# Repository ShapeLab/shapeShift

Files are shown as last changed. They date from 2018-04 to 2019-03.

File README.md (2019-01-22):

## shapeShift: 2D Spatial Manipulation and Self-Actuation of Tabletop Shape Displays for Tangible and Haptic Interaction 

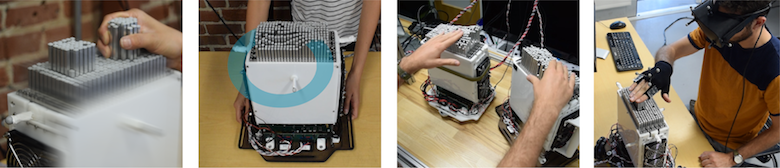
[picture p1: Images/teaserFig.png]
Teaser


We explore interactions enabled by 2D spatial manipulation and self-actuation of a tabletop shape display. To explore these interactions, we developed shapeShift, a compact, high-resolution (7 mm pitch), mobile tabletop shape display. shapeShift can be mounted on passive rollers allowing for bimanual interaction where the user can freely manipulate the system while it renders spatially relevant content. shapeShift can also be mounted on an omnidirectional-robot to provide both vertical and lateral kinesthetic feedback, display moving objects, or act as an encountered-type haptic device for VR. We present a study on haptic search tasks comparing spatial manipulation of a shape display for egocentric exploration of a map versus exploration using a fixed display and a touch pad. Results show a 30% decrease in navigation path lengths, 24% decrease in task time, 15% decrease in mental demand and 29% decrease in frustration in favor of egocentric navigation. 

[Watch a video](https://www.youtube.com/embed/Z6LSsJoDdtY/0.jpg) or read more at the [shape lab website](http://shape.stanford.edu/research/shapeShift/)

### Technical Implementation
<p align="center">
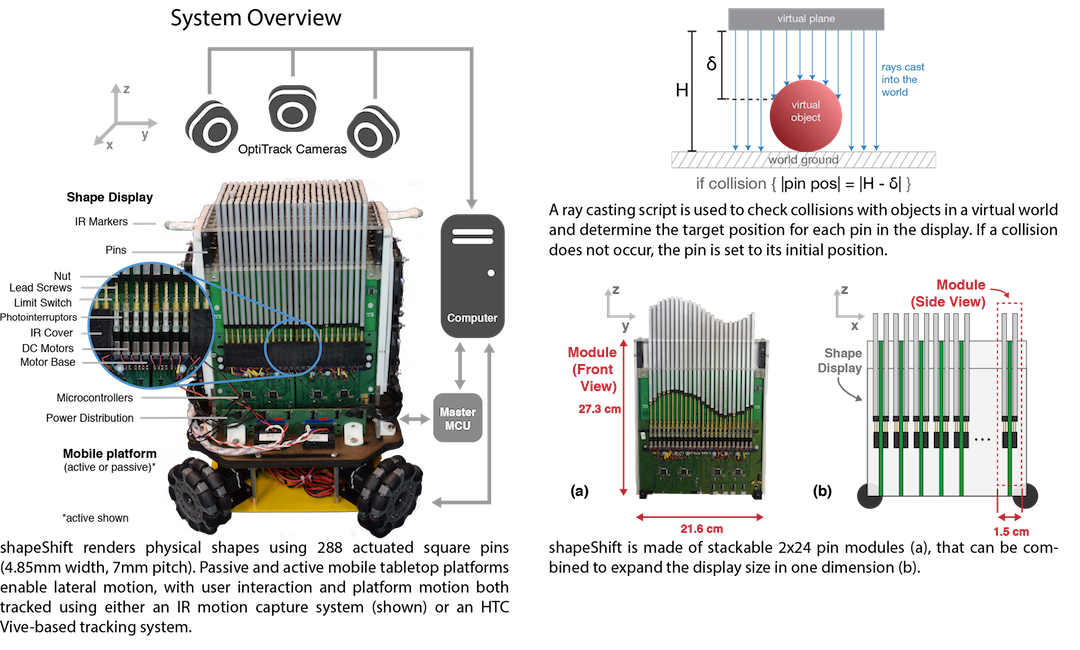
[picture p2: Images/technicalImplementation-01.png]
exploded
	
</p>

### Getting started
CAD, PCB, firmware and software files are provided. Detailed instructions and link to BOM can be found in [these slides](https://docs.google.com/presentation/d/1R9Z0mCOPYOkJPzbJNwtG9fEYhSLC97248hX_nJxPLbI/edit?usp=sharing).

### Latest Updates
- Released PCB + CAD files + Firmware
- Unity software coming soon

### Authors
[Alexa F. Siu](http://alexasiu.com), Eric J. Gonzalez, Shenli Yuan, Jason B. Ginsberg, and Sean Follmer

### Contact
Raise a new [issue](https://github.com/ShapeLab/shapeShift/issues) or contact me at afsiu@stanford.edu

<br>

<p align="center">
	<br />This work is licensed under a <a rel="license" href="http://creativecommons.org/licenses/by-nc/4.0/">Creative Commons Attribution-NonCommercial 4.0 International License</a>.
</p>

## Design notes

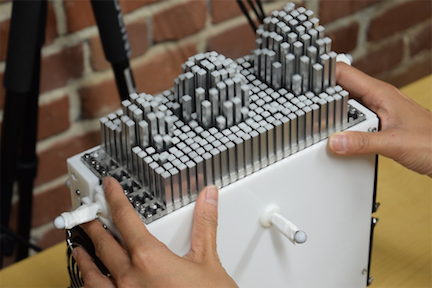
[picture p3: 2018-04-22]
Images/main.png

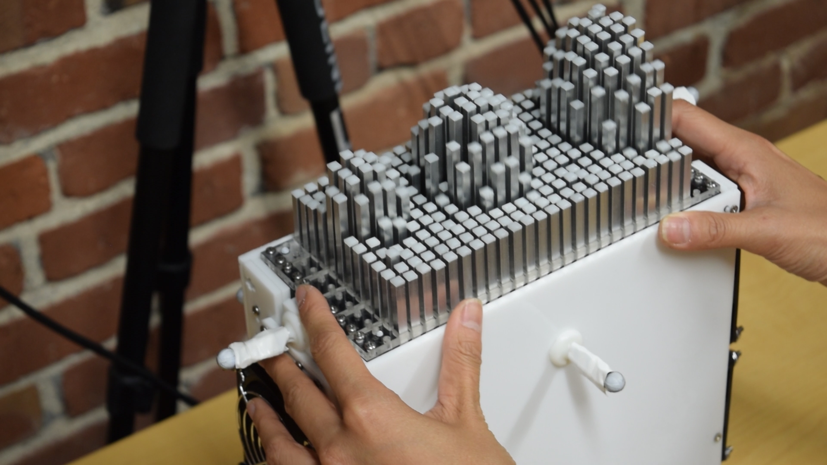
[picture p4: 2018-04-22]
Images/main3.png

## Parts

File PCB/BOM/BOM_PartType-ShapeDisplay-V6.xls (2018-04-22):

Comment | Description | Designator | Footprint | LibRef | Quantity | Comment
Murata GRM155R71C104KA88J | Multilayer Ceramic Capacitors MLCC - SMD/SMT 0.1uF 16 volts 10% | C1, C2_SH1, C2_SH2, C2_SH3, C2_SH4, C2_SH5, C2_SH6, C2_SH7, C2_SH8, C2_SH9, C2_SH10, C2_SH11, C2_SH12, C2_SH13, C2_SH14, C2_SH15, C2_SH16, C2_SH17, C2_SH18, C2_SH19, C2_SH20, C2_SH21, C2_SH22, C2_SH23, C2_SH24, C2_SH25, C2_SH26, C2_SH27, C2_SH28, C2_SH29, C2_SH30, C2_SH31, C2_SH32, C2_SH33, C2_SH34, C2_SH35, C2_SH36, C2_SH37, C2_SH38, C2_SH39, C2_SH40, C2_SH41, C2_SH42, C2_SH43, C2_SH44, C2_SH45, C2_SH46, C2_SH47, C2_SH48, C3_SH1, C3_SH2, C3_SH3, C3_SH4, C3_SH5, C3_SH6, C3_SH7, C3_SH8, C3_SH9, C3_SH10, C3_SH11, C3_SH12, C3_SH13, C3_SH14, C3_SH15, C3_SH16, C3_SH17, C3_SH18, C3_SH19, C3_SH20, C3_SH21, C3_SH22, C3_SH23, C3_SH24, C3_SH25, C3_SH26, C3_SH27, C3_SH28, C3_SH29, C3_SH30, C3_SH31, C3_SH32, C3_SH33, C3_SH34, C3_SH35, C3_SH36, C3_SH37, C3_SH38, C3_SH39, C3_SH40, C3_SH41, C3_SH42, C3_SH43, C3_SH44, C3_SH45, C3_SH46, C3_SH47, C3_SH48, C7, C8, C9, C11, C12, C13, C14, C15, C18, C19, C20, C21, C22, C23, C24, C26, C28, C29, C30, C32, C33, C34, C36, C37, C39, C40, C41, C42, C301 | CAPC1005X55X25NL05T10 | CMP-131530-4, CMP-131530-5, CMP-131530-5, CMP-131530-5, CMP-131530-5, CMP-131530-5, CMP-131530-5, CMP-131530-5, CMP-131530-5, CMP-131530-5, CMP-131530-5, CMP-131530-5, CMP-131530-5, CMP-131530-5, CMP-131530-5, CMP-131530-5, CMP-131530-5, CMP-131530-5, CMP-131530-5, CMP-131530-5, CMP-131530-5, CMP-131530-5, CMP-131530-5, CMP-131530-5, CMP-131530-5, CMP-131530-5, CMP-131530-5, CMP-131530-5, CMP-131530-5, CMP-131530-5, CMP-131530-5, CMP-131530-5, CMP-131530-5, CMP-131530-5, CMP-131530-5, CMP-131530-5, CMP-131530-5, CMP-131530-5, CMP-131530-5, CMP-131530-5, CMP-131530-5, CMP-131530-5, CMP-131530-5, CMP-131530-5, CMP-131530-5, CMP-131530-5, CMP-131530-5, CMP-131530-5, CMP-131530-5, CMP-131530-4, CMP-131530-4, CMP-131530-4, CMP-131530-4, CMP-131530-4, CMP-131530-4, CMP-131530-4, CMP-131530-4, CMP-131530-4, CMP-131530-4, CMP-131530-4, CMP-131530-4, CMP-131530-4, CMP-131530-4, CMP-131530-4, CMP-131530-4, CMP-131530-4, CMP-131530-4, CMP-131530-4, CMP-131530-4, CMP-131530-4, CMP-131530-4, CMP-131530-4, CMP-131530-4, CMP-131530-4, CMP-131530-4, CMP-131530-4, CMP-131530-4, CMP-131530-4, CMP-131530-4, CMP-131530-4, CMP-131530-4, CMP-131530-4, CMP-131530-4, CMP-131530-4, CMP-131530-4, CMP-131530-4, CMP-131530-4, CMP-131530-4, CMP-131530-4, CMP-131530-4, CMP-131530-4, CMP-131530-4, CMP-131530-4, CMP-131530-4, CMP-131530-4, CMP-131530-4, CMP-131530-4, CMP-131530-4, CMP-131530-4, CMP-131530-4, CMP-131530-4, CMP-131530-4, CMP-131530-4, CMP-131530-4, CMP-131530-4, CMP-131530-4, CMP-131530-4, 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 | 126
Kemet T491D107K010AT | Capacitor, Tantalum, 100 uF, +/- 10%, -55 to 125 degC, 2-Pin SMD, RoHS, Tape and Reel | C4, C5 | KEMT-T491-D_M | CMP-19303020-3 | 2
AVX Interconnect / Elco 04024D225MAT2A | Multilayer Ceramic Capacitors MLCC - SMD/SMT 0402 2.2uF 4volts Z5U 20% | C6, C10, C16, C17, C25, C27, C31, C35 | CAPC1005X56X25NL10T15 | CMP-126964-2 | 8
Murata GRM155R60E106ME16D | MURATA GRM155R60E106ME16D CAP, MLCC, X5R, 10UF, 2.5V, 0402 | C38_M1, C38_M2, C38_M3, C38_M4, C38_M5, C38_M6, C38_M7, C38_M8, C38_M9, C38_M10, C38_M11, C38_M12 | CAPC1005X55X25LL05T10 | CMP-4845683-2 | 12
Murata GRM188R61A105KA61D | Cap Ceramic 1uF 10V X5R 10% SMD 0603 85°C Paper T/R | C300 | PCB-5ad2x2bi7uvqy4h6r523-1 | CMP-bc9f7597675b6358-1 | 1
Avago HSMA-C190 | LED 595NM AMB DIFF 0603 SMD | DS1, DS2, DS3, DS4 | AVAG-HSMX-C190 | CMP-1545179-2 | 4
BLM18AG601SN1D | Chip Ferrite Bead for General Use, 600 Ohm, 500 mA, -55 to 125 degC, 1.6 x 0.8 x 0.95 mm SMD, Tape and Reel | FB1, FB2, FB3, FB4, FB5, FB6, FB7, FB8 | MURA-BLM18-F-H1-CHIP-2_V | CMP-14419471-3 | 8
Motor Pads (DO NOT PLACE) | 0.1 Motor Header" | P1_M1, P1_M2, P1_M3, P1_M4, P1_M5, P1_M6, P1_M7, P1_M8, P1_M9, P1_M10, P1_M11, P1_M12, P2_M1, P2_M2, P2_M3, P2_M4, P2_M5, P2_M6, P2_M7, P2_M8, P2_M9, P2_M10, P2_M11, P2_M12 | PCB-xvvcuqhn1e5czmkfuo8y-1 | CMP-8f9uj9jvfkpvtxocz57i-8 | 24 | Do not place this component. These are just solder pads for the motor thus there is no associated component required for PCB pick and place
Molex 504050-0491 | 1, 50mm Pitch Pico-Lock Surface Mount Wire-to-Board Header, Right Angle, 2, 00mm Mated Height, Positive Side Locks, 4... | P3, P4 | PCB-3hbjo6f1kjza7fe1cyp7-1 | CMP-a06768b592477fa0-1 | 2
Molex 504050-0691 | Conn Wire to Board HDR 6 POS 1.5mm Solder RA SMD Pico-Lock? ????? ? T/R | PP1 | PCB-qm61l72v4f69z34pnmbq-1 | CMP-6c2ba4f309ebb3ec-1 | 1
Sharp GP2S60 | GP2S Series 0.5 mm 930 nm 35 V 50 mA SMT Compact Reflective Photointerrupter | Q1_SH1, Q1_SH2, Q1_SH3, Q1_SH4, Q1_SH5, Q1_SH6, Q1_SH7, Q1_SH8, Q1_SH9, Q1_SH10, Q1_SH11, Q1_SH12, Q1_SH13, Q1_SH14, Q1_SH15, Q1_SH16, Q1_SH17, Q1_SH18, Q1_SH19, Q1_SH20, Q1_SH21, Q1_SH22, Q1_SH23, Q1_SH24, Q1_SH25, Q1_SH26, Q1_SH27, Q1_SH28, Q1_SH29, Q1_SH30, Q1_SH31, Q1_SH32, Q1_SH33, Q1_SH34, Q1_SH35, Q1_SH36, Q1_SH37, Q1_SH38, Q1_SH39, Q1_SH40, Q1_SH41, Q1_SH42, Q1_SH43, Q1_SH44, Q1_SH45, Q1_SH46, Q1_SH47, Q1_SH48 | PCB-8czhrdy28ouaryjd2oxu-1 | CMP-2bace0f94d51f46b-9 | 48
Panasonic / Panasonic ECG ERJ-2RKF1003X | Resistor Thick Film 0402 100k Ohm 1% 1-10 Watt ±100ppm °C Surface Mount Punched Carrier Tape and Reel | R1, R20_SH1, R20_SH2, R20_SH3, R20_SH4, R20_SH5, R20_SH6, R20_SH7, R20_SH8, R20_SH9, R20_SH10, R20_SH11, R20_SH12, R20_SH13, R20_SH14, R20_SH15, R20_SH16, R20_SH17, R20_SH18, R20_SH19, R20_SH20, R20_SH21, R20_SH22, R20_SH23, R20_SH24, R20_SH25, R20_SH26, R20_SH27, R20_SH28, R20_SH29, R20_SH30, R20_SH31, R20_SH32, R20_SH33, R20_SH34, R20_SH35, R20_SH36, R20_SH37, R20_SH38, R20_SH39, R20_SH40, R20_SH41, R20_SH42, R20_SH43, R20_SH44, R20_SH45, R20_SH46, R20_SH47, R20_SH48, R200 | 0402R | CMP-3656264-6 | 50
Panasonic / Panasonic ECG ERJ-2RKF1002X | Res Thick Film 0402 10K Ohm 1% 0.1W(1/10W) ±100ppm/°C Molded SMD Punched Carrier T/R | R3, R4, R5, R6, R7, R8, R9, R10, R11, R12, R13, R14, R23 | 0402-RES | CMP-4843210-4 | 13
Panasonic ERJ-2RKF4702X | Res Thick Film 0402 47K Ohm 1% 0.1W(1/10W) ±100ppm/C Molded SMD Automotive Punched T/R | R15_SH1, R15_SH2, R15_SH3, R15_SH4, R15_SH5, R15_SH6, R15_SH7, R15_SH8, R15_SH9, R15_SH10, R15_SH11, R15_SH12, R15_SH13, R15_SH14, R15_SH15, R15_SH16, R15_SH17, R15_SH18, R15_SH19, R15_SH20, R15_SH21, R15_SH22, R15_SH23, R15_SH24, R15_SH25, R15_SH26, R15_SH27, R15_SH28, R15_SH29, R15_SH30, R15_SH31, R15_SH32, R15_SH33, R15_SH34, R15_SH35, R15_SH36, R15_SH37, R15_SH38, R15_SH39, R15_SH40, R15_SH41, R15_SH42, R15_SH43, R15_SH44, R15_SH45, R15_SH46, R15_SH47, R15_SH48 | PCB-tt2uar11avl7c0hq0m8y-1 | CMP-8bf24267710c5435-2 | 48
Panasonic ERJ-2GEJ224X | Thick Film Resistors - SMD 0402 220Kohms 5% Tol | R16_SH1, R16_SH2, R16_SH3, R16_SH4, R16_SH5, R16_SH6, R16_SH7, R16_SH8, R16_SH9, R16_SH10, R16_SH11, R16_SH12, R16_SH13, R16_SH14, R16_SH15, R16_SH16, R16_SH17, R16_SH18, R16_SH19, R16_SH20, R16_SH21, R16_SH22, R16_SH23, R16_SH24, R16_SH25, R16_SH26, R16_SH27, R16_SH28, R16_SH29, R16_SH30, R16_SH31, R16_SH32, R16_SH33, R16_SH34, R16_SH35, R16_SH36, R16_SH37, R16_SH38, R16_SH39, R16_SH40, R16_SH41, R16_SH42, R16_SH43, R16_SH44, R16_SH45, R16_SH46, R16_SH47, R16_SH48 | RESC1005X40X25NL05T05 | CMP-3655892-2 | 48
Panasonic ERJ-2GEJ332X | Thick Film Resistors - SMD 0402 3.3Kohms 5% Tol | R17_SH1, R17_SH2, R17_SH3, R17_SH4, R17_SH5, R17_SH6, R17_SH7, R17_SH8, R17_SH9, R17_SH10, R17_SH11, R17_SH12, R17_SH13, R17_SH14, R17_SH15, R17_SH16, R17_SH17, R17_SH18, R17_SH19, R17_SH20, R17_SH21, R17_SH22, R17_SH23, R17_SH24, R17_SH25, R17_SH26, R17_SH27, R17_SH28, R17_SH29, R17_SH30, R17_SH31, R17_SH32, R17_SH33, R17_SH34, R17_SH35, R17_SH36, R17_SH37, R17_SH38, R17_SH39, R17_SH40, R17_SH41, R17_SH42, R17_SH43, R17_SH44, R17_SH45, R17_SH46, R17_SH47, R17_SH48, R44_SW1, R44_SW2, R44_SW3, R44_SW4, R44_SW5, R44_SW6, R44_SW7, R44_SW8, R44_SW9, R44_SW10, R44_SW11, R44_SW12, R44_SW13, R44_SW14, R44_SW15, R44_SW16, R44_SW17, R44_SW18, R44_SW19, R44_SW20, R44_SW21, R44_SW22, R44_SW23, R44_SW24 | RESC1005X40X25NL05T05 | CMP-3655114-2 | 72
Panasonic ERJ-2GEJ274X | Thick Film Resistors - SMD 0402 270Kohms 5% Tol | R18_SH1, R18_SH2, R18_SH3, R18_SH4, R18_SH5, R18_SH6, R18_SH7, R18_SH8, R18_SH9, R18_SH10, R18_SH11, R18_SH12, R18_SH13, R18_SH14, R18_SH15, R18_SH16, R18_SH17, R18_SH18, R18_SH19, R18_SH20, R18_SH21, R18_SH22, R18_SH23, R18_SH24, R18_SH25, R18_SH26, R18_SH27, R18_SH28, R18_SH29, R18_SH30, R18_SH31, R18_SH32, R18_SH33, R18_SH34, R18_SH35, R18_SH36, R18_SH37, R18_SH38, R18_SH39, R18_SH40, R18_SH41, R18_SH42, R18_SH43, R18_SH44, R18_SH45, R18_SH46, R18_SH47, R18_SH48 | RESC1005X40X25NL05T05 | CMP-3652051-2 | 48
Panasonic ERJ-2GEJ181X | Thick Film Resistors - SMD 0402 180ohms 5% Tol | R19_SH1, R19_SH2, R19_SH3, R19_SH4, R19_SH5, R19_SH6, R19_SH7, R19_SH8, R19_SH9, R19_SH10, R19_SH11, R19_SH12, R19_SH13, R19_SH14, R19_SH15, R19_SH16, R19_SH17, R19_SH18, R19_SH19, R19_SH20, R19_SH21, R19_SH22, R19_SH23, R19_SH24, R19_SH25, R19_SH26, R19_SH27, R19_SH28, R19_SH29, R19_SH30, R19_SH31, R19_SH32, R19_SH33, R19_SH34, R19_SH35, R19_SH36, R19_SH37, R19_SH38, R19_SH39, R19_SH40, R19_SH41, R19_SH42, R19_SH43, R19_SH44, R19_SH45, R19_SH46, R19_SH47, R19_SH48 | RESC1005X40X25NL05T05 | CMP-3654900-2 | 48
Panasonic ERJ-2GEJ684X | Thick Film Resistors - SMD 0402 680Kohms 5% Tol | R21_SH1, R21_SH2, R21_SH3, R21_SH4, R21_SH5, R21_SH6, R21_SH7, R21_SH8, R21_SH9, R21_SH10, R21_SH11, R21_SH12, R21_SH13, R21_SH14, R21_SH15, R21_SH16, R21_SH17, R21_SH18, R21_SH19, R21_SH20, R21_SH21, R21_SH22, R21_SH23, R21_SH24, R21_SH25, R21_SH26, R21_SH27, R21_SH28, R21_SH29, R21_SH30, R21_SH31, R21_SH32, R21_SH33, R21_SH34, R21_SH35, R21_SH36, R21_SH37, R21_SH38, R21_SH39, R21_SH40, R21_SH41, R21_SH42, R21_SH43, R21_SH44, R21_SH45, R21_SH46, R21_SH47, R21_SH48 | RESC1005X40X25NL05T05 | CMP-3654133-2 | 48
Panasonic ERJ-2GEJ124X | Thick Film Resistors - SMD 0402 120Kohms 5% Tol | R22_SH1, R22_SH2, R22_SH3, R22_SH4, R22_SH5, R22_SH6, R22_SH7, R22_SH8, R22_SH9, R22_SH10, R22_SH11, R22_SH12, R22_SH13, R22_SH14, R22_SH15, R22_SH16, R22_SH17, R22_SH18, R22_SH19, R22_SH20, R22_SH21, R22_SH22, R22_SH23, R22_SH24, R22_SH25, R22_SH26, R22_SH27, R22_SH28, R22_SH29, R22_SH30, R22_SH31, R22_SH32, R22_SH33, R22_SH34, R22_SH35, R22_SH36, R22_SH37, R22_SH38, R22_SH39, R22_SH40, R22_SH41, R22_SH42, R22_SH43, R22_SH44, R22_SH45, R22_SH46, R22_SH47, R22_SH48 | RESC1005X40X25NL05T05 | CMP-3655784-2 | 48
Panasonic ERA-2AED332X | Res Thin Film 0402 3.3K Ohm 0.5% 1/16W ±25ppm/C Molded SMD Punched Carrier T/R | R24, R25 | RESC1005X40X25ML10T10 | CMP-1850617-2 | 2
Panasonic ERA-2AED471X | Res Thin Film 0402 470 Ohm 0.5% 1/16W ±25ppm/C Molded SMD Punched Carrier T/R | R26, R27, R34, R35 | RESC1005X40X25ML10T10 | CMP-1850669-2 | 4
Panasonic ERJ-2RKF33R0X | Res Thick Film 0402 33 Ohm 1% 0.1W(1/10W) ±100ppm/C Molded SMD Automotive Punched T/R | R28, R29, R30, R31, R36, R37, R38, R39 | RESC1005X40X25NL05T05 | CMP-8f7846cd438750bf-1 | 8
Panasonic ERA-2AED470X | Res Thin Film 0402 47 Ohm 0.5% 1/16W 25ppm/C Molded SMD Punched Carrier T/R | R32, R33, R40, R41 | RESC1005X40X25ML10T10 | CMP-1850631-2 | 4
Panasonic ERA-2AED121X | Res Thin Film 0402 120 Ohm 0.5% 1/16W ±25ppm/C Molded SMD Punched Carrier T/R | R42, R43 | RESC1005X40X25ML10T10 | CMP-1850636-2 | 2 | Do not place this component unless want capacitive touch
TE Connectivity 1447009-5 | Type Y Spring Finger 0820 Nickel Finish for Mobile Phone | SP1_TK1, SP1_TK2, SP1_TK3, SP1_TK4, SP1_TK5, SP1_TK6, SP1_TK7, SP1_TK8, SP1_TK9, SP1_TK10, SP1_TK11, SP1_TK12, SP2_TK1, SP2_TK2, SP2_TK3, SP2_TK4, SP2_TK5, SP2_TK6, SP2_TK7, SP2_TK8, SP2_TK9, SP2_TK10, SP2_TK11, SP2_TK12 | PCB-e361hi4gnwrtm5zk832i-1 | CMP-c2a40909d15d1d63-4 | 24 | Do not place this component unless want capacitive touch
Omron D3SH-A0L | Switch Detector N.O. SPST Lever J-Bend 0.001A 5VDC SMD Embossed T/R | SW1_SW1, SW1_SW2, SW1_SW3, SW1_SW4, SW1_SW5, SW1_SW6, SW1_SW7, SW1_SW8, SW1_SW9, SW1_SW10, SW1_SW11, SW1_SW12, SW1_SW13, SW1_SW14, SW1_SW15, SW1_SW16, SW1_SW17, SW1_SW18, SW1_SW19, SW1_SW20, SW1_SW21, SW1_SW22, SW1_SW23, SW1_SW24 | PCB-84ze8qnb4ube2ntai06t-1 | CMP-b958700038a9669f-6 | 24
Omron B3U-1000P | Switch Tactile N.O. SPST Round Button Gull Wing 0.05A 12VDC 1.5N SMD Embossed T/R | SW_R1, SW_R2, SW_R3, SW_R4 | PCB-a8ildroimidtkya2dspy-1 | CMP-2198857-6 | 4
AT42QT2120X-XU | QTouch 12-channel Touch Sensor IC, -40° to +85° C, 20-Pin TSSOP | U1 | 20X_N | CMP-4868163-2 | 1
NCS2200SN1T1G | Low Voltage Comparator, 0.85 to 6 V, -40 to 105 degC, 5-Pin TSOP, Pb-Free, Tape and Reel | U2_SH1, U2_SH2, U2_SH3, U2_SH4, U2_SH5, U2_SH6, U2_SH7, U2_SH8, U2_SH9, U2_SH10, U2_SH11, U2_SH12, U2_SH13, U2_SH14, U2_SH15, U2_SH16, U2_SH17, U2_SH18, U2_SH19, U2_SH20, U2_SH21, U2_SH22, U2_SH23, U2_SH24, U2_SH25, U2_SH26, U2_SH27, U2_SH28, U2_SH29, U2_SH30, U2_SH31, U2_SH32, U2_SH33, U2_SH34, U2_SH35, U2_SH36, U2_SH37, U2_SH38, U2_SH39, U2_SH40, U2_SH41, U2_SH42, U2_SH43, U2_SH44, U2_SH45, U2_SH46, U2_SH47, U2_SH48 | ONSC-TSOP-5-483-02_V | CMP-1344714-2 | 48
LP3872EMP-3.3/NOPB | 1.5A Fast Ultra Low Dropout Linear Regulator, 5-pin SOT-223, Pb-Free | U3 | MP05A_M | CMP-1498683-3 | 1
Freescale MK20DX256VLH7 | ARM Microcontrollers - MCU KINETIS 256K | U4, U5, U8, U10 | MCHP-TQFP-PT64_M | CMP-3247417-10 | 4
Freescale Semiconductor MKL02Z32VFG4 | 32 Bit Microcontroller, Kinetis L Series Ultra Low Power, ARM Cortex-M0+, 48 MHz, 32 KB, 4 KB, 16 | U6, U7, U9, U11 | PCB-x9mqhsnmps9pb7u4805l-1 | CMP-20f6e874a12cff31-1 | 4 | This microcontroller is purchased pre-programmed from PJRC: https://www.pjrc.com/store/ic_mkl02.html
Allegro MicroSystems A3901SEJTR-T | ALLEGRO MICROSYSTEMS A3901SEJTR-T MOTOR DRIV FULL BRIDGE, 400MA, DFN-10 | U12_M1, U12_M2, U12_M3, U12_M4, U12_M5, U12_M6, U12_M7, U12_M8, U12_M9, U12_M10, U12_M11, U12_M12 | A3901 | CMP-966393-6 | 12
Maxim Integrated MAX3465ESD+T | Single Transmitter/Receiver RS-422/RS-485 14-Pin SOIC N T/R | U13, U14, U15, U16 | PCB-0pjqd4tle5vuu6cq43w1-1 | CMP-16bddd239dd2c97a-2 | 4
Hirose ZX62-AB-5PA(31) | ZX Series 5 Position Horizontal Right Angle Micro-AB USB 2.0 Connector | USB1, USB2, USB3, USB4 | PCB-6fpoyl2s54pfe2ixpvl9-1 | CMP-82274f6eb75a5de0-1 | 4
ECS International ECS-160-8-30B-CKM | Crystal 16.0000mhz 8pf Smd | Y1, Y2, Y3, Y4 | Resistor | CMP-ac9364da4e867354-7 | 4

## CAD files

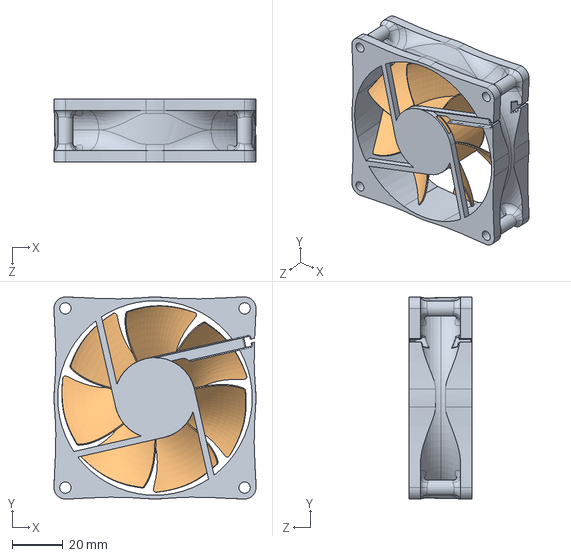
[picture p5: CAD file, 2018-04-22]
CAD/External Components/80mm PC fan.SLDASM
80.0 x 80.0 x 25.0 mm
Outer ring
FAn 1

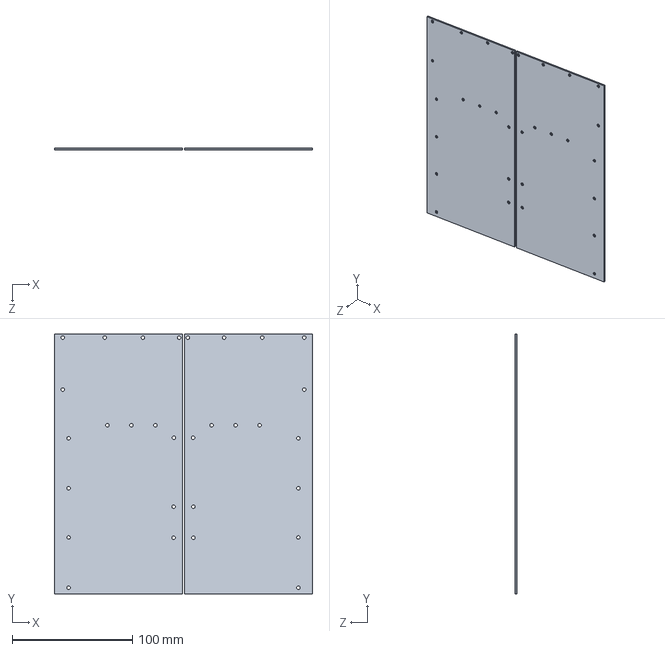
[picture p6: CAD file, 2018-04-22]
CAD/PCB Assembly/PCB-Assembly.SLDASM
214.8 x 216.2 x 1.67 mm
Board x 4

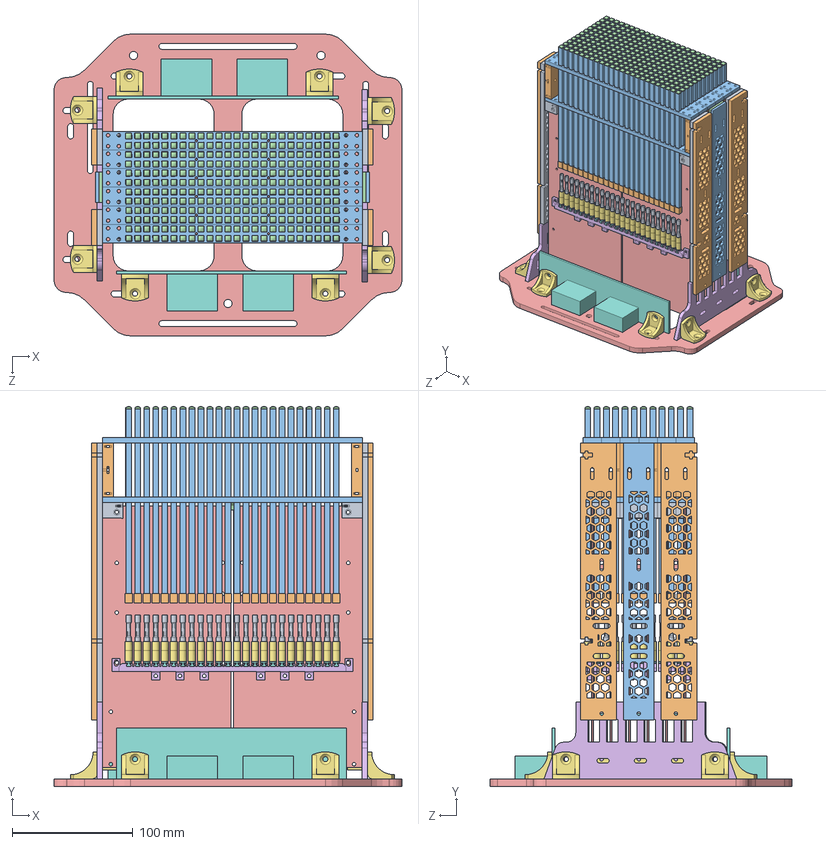
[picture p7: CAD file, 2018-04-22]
CAD/OverallAssembly.SLDASM
287.7 x 314.3 x 249.6 mm
TopSupportBracket x 12
TopSupportSpacer x 12
TopSupportGrid x 12
bridgeSupport x 6
Board x 24
motorBase x 12
microMotor x 288
motorAttachment x 288
shaftAdapter x 288
nut x 288
pin x 288
pinTop x 288
bracketBlockTop x 6
bracketBlockBottomMiddle x 3
bracketBlockBottomEdge x 6
bracketBlockMiddle x 3
InnerEdge-ModuleWall x 4
OuterEdge-ModuleWall x 4
OuterMiddle-ModuleWall x 2
InnerMiddle-ModuleWall x 2
BasePlate
BaseWall x 2
13135A590_BRACKET-PDB x 8
PowerDistributionBoard (PDB) x 2

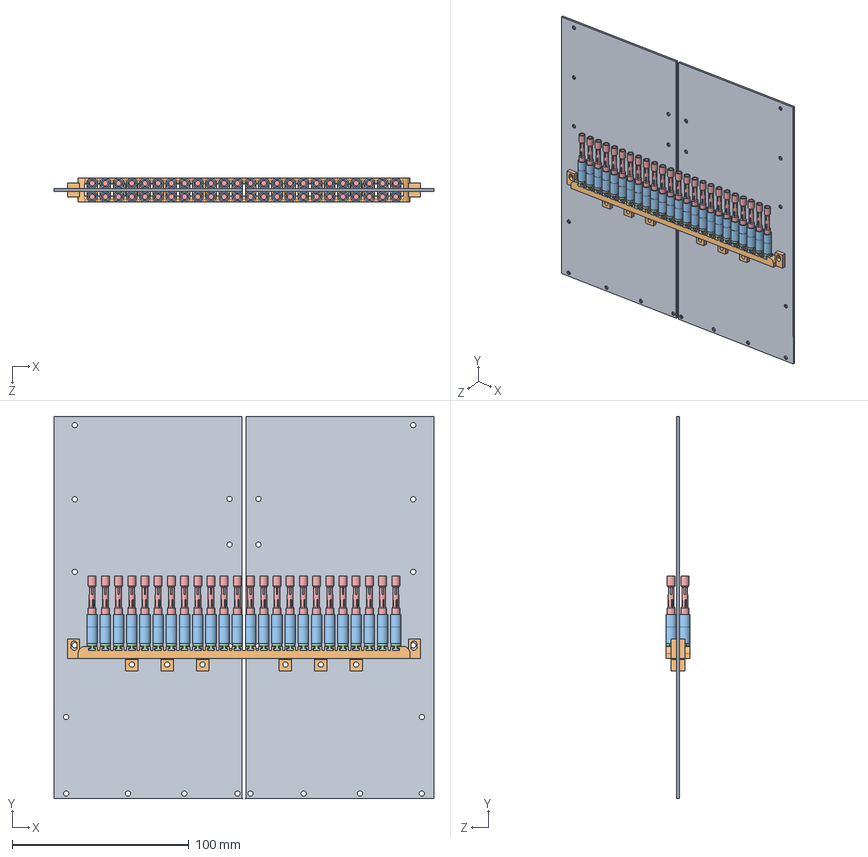
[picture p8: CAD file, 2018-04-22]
CAD/PCB Assembly/PCB-Motors-Assembly.sldasm
214.8 x 216.2 x 13.7 mm
Board x 4
motorBase x 2
microMotor x 48
motorAttachment x 48
shaftAdapter x 48

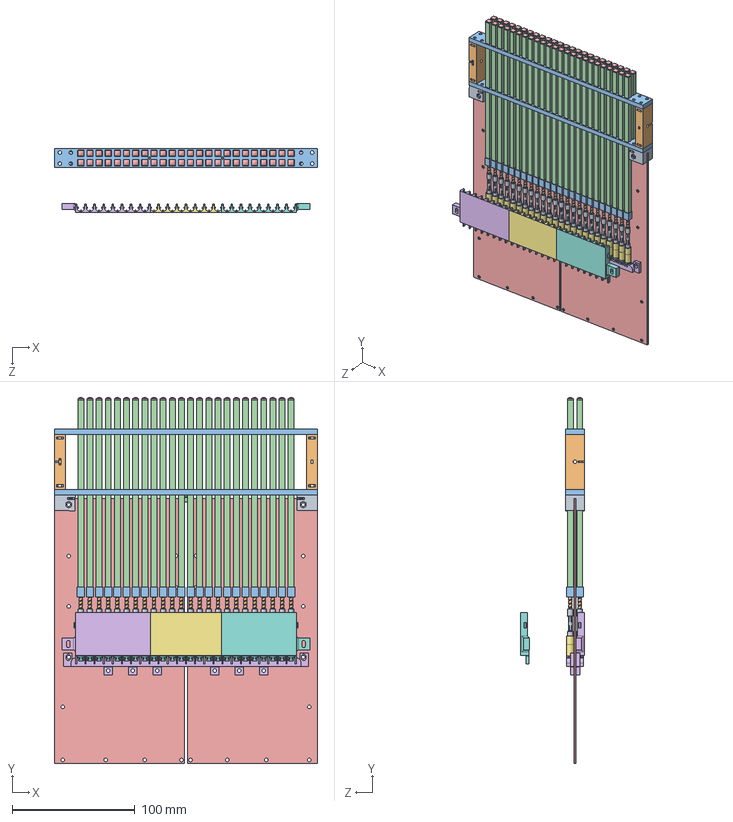
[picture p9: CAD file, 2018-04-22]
CAD/PCB-Motors-Support-Assembly.sldasm
214.8 x 298.6 x 52.5 mm
TopSupportBracket x 2
TopSupportSpacer x 2
TopSupportGrid x 2
bridgeSupport
Board x 4
motorBase x 2
microMotor x 48
motorAttachment x 48
shaftAdapter x 48
leadscrew x 48
nut x 48
pin x 48
pinTop x 48
motorCover_Left x 2
motorCover_Middle x 2
motorCover_Right x 2

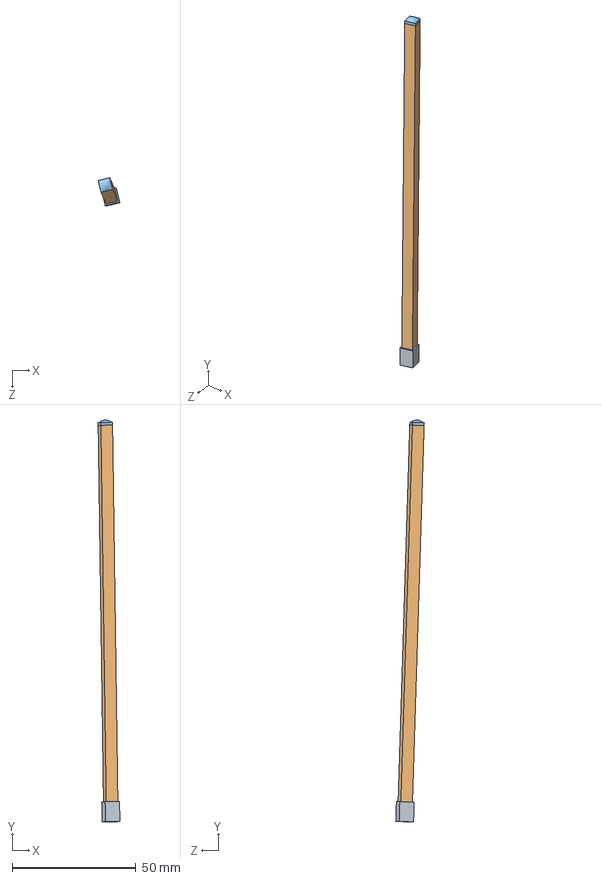
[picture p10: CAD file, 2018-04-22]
CAD/Actuator Unit/nutPinAssembly.SLDASM
8.82 x 162.6 x 11.5 mm
nut
pin
pinTop

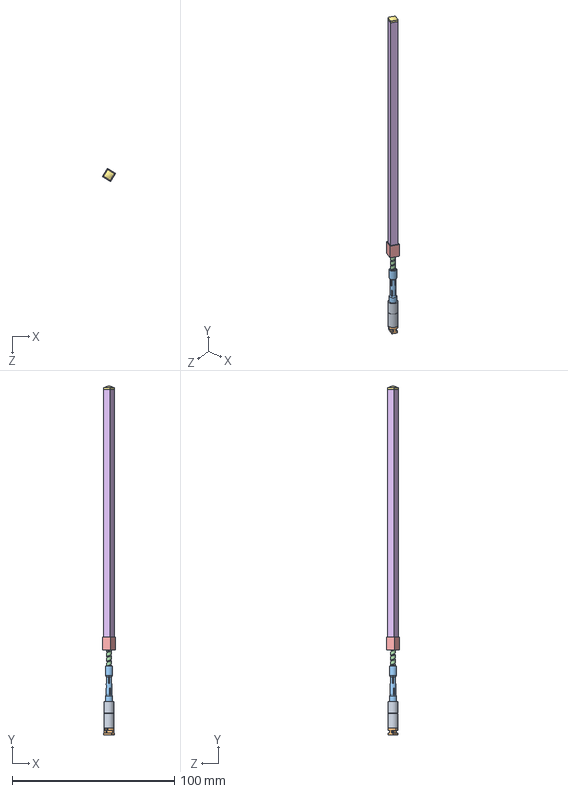
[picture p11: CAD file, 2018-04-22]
CAD/Actuator Unit/microMotorAssembly.SLDASM
8.28 x 214.9 x 8.28 mm
microMotor
motorAttachment
shaftAdapter
leadscrew
nut
pin
pinTop

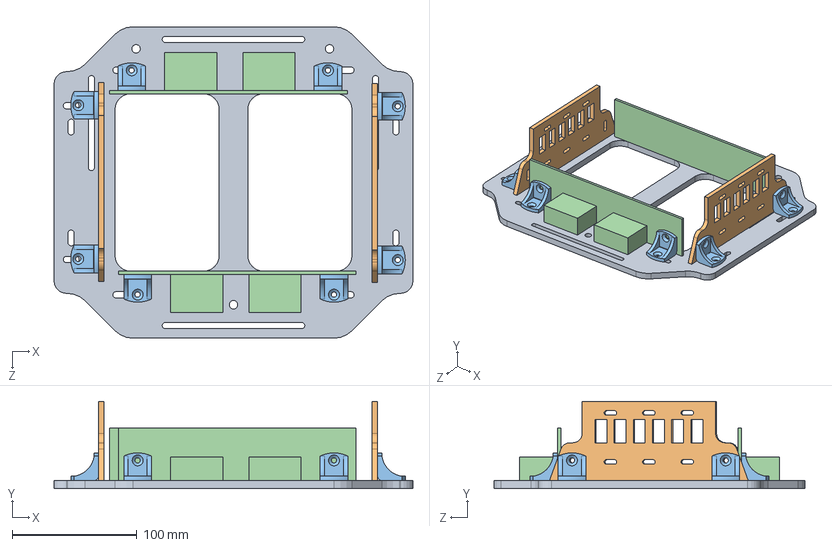
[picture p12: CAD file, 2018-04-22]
CAD/BaseAssembly.SLDASM
287.7 x 69.9 x 249.6 mm
BasePlate
BaseWall x 2
13135A590_BRACKET-PDB x 8
PowerDistributionBoard (PDB) x 2

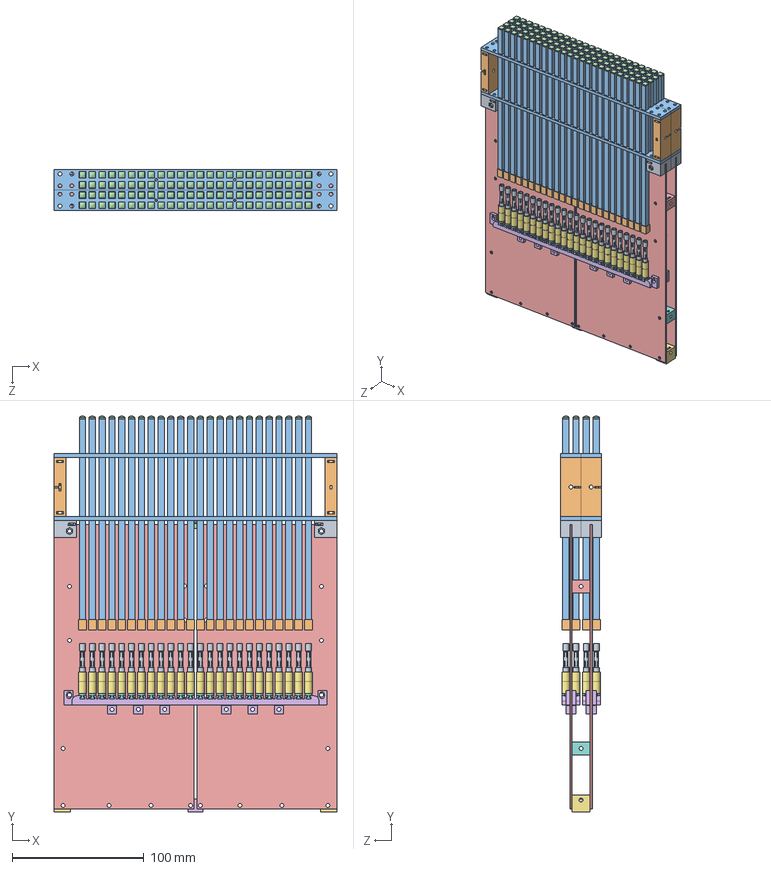
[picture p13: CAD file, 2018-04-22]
CAD/ModuleAssembly.SLDASM
214.8 x 300.7 x 30.8 mm
TopSupportBracket x 4
TopSupportSpacer x 4
TopSupportGrid x 4
bridgeSupport x 2
Board x 8
motorBase x 4
microMotor x 96
motorAttachment x 96
shaftAdapter x 96
nut x 96
pin x 96
pinTop x 96
bracketBlockTop x 2
bracketBlockBottomMiddle
bracketBlockBottomEdge x 2
bracketBlockMiddle

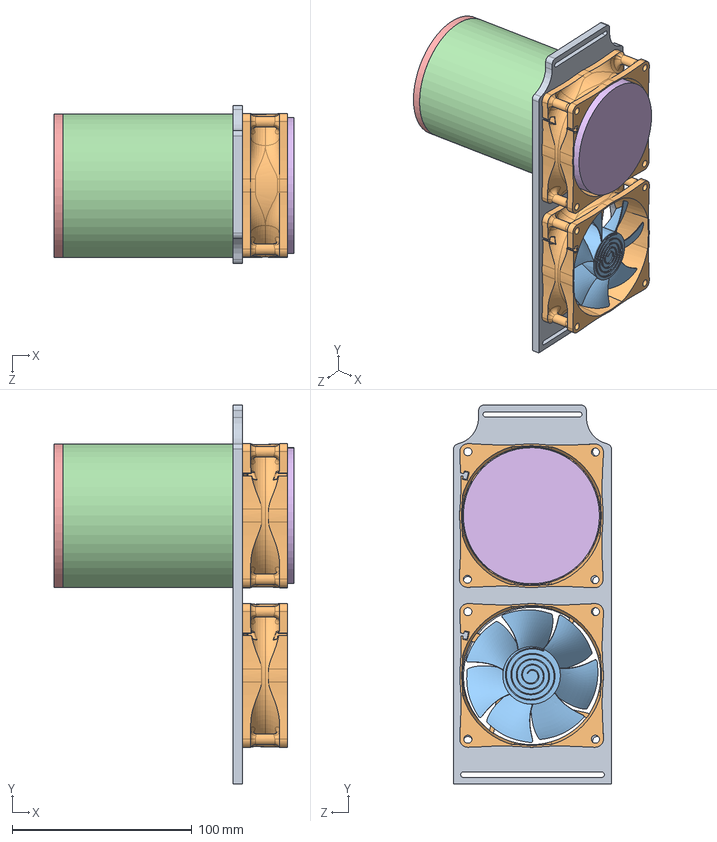
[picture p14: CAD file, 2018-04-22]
CAD/FanWallAssembly.SLDASM
133.6 x 211.0 x 88.0 mm
FanMount-Wall
Outer ring x 2
FAn 1 x 2

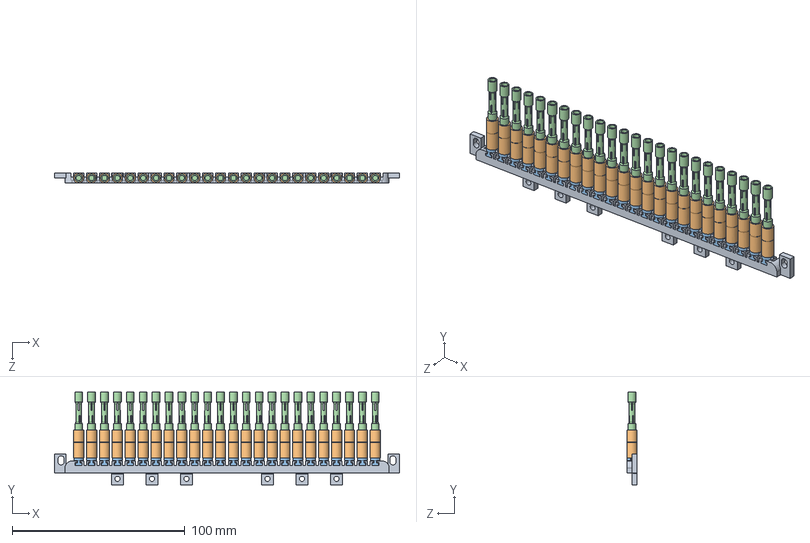
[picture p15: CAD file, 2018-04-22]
CAD/motorBaseAssembly.SLDASM
199.7 x 53.7 x 6.00 mm
motorBase
microMotor x 24
motorAttachment x 24
shaftAdapter x 24

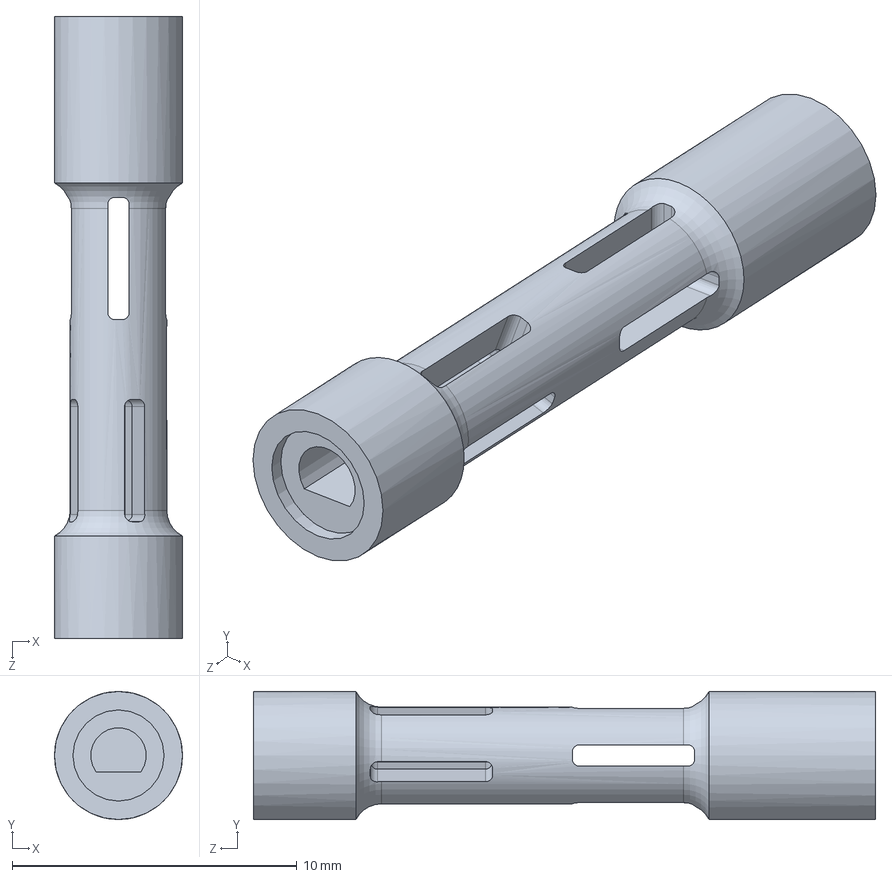
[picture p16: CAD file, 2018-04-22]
CAD/Actuator Unit/shaftAdapter.SLDPRT
4.50 x 4.50 x 21.8 mm

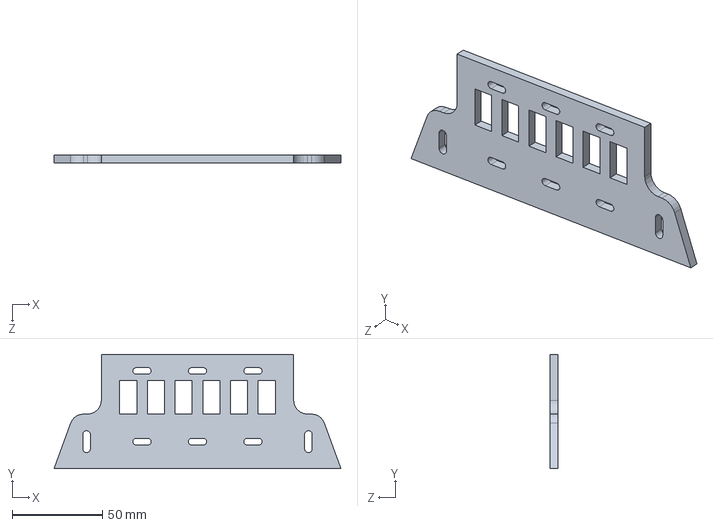
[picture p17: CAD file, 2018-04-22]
CAD/Base Components/BaseWall.SLDPRT
159.4 x 63.5 x 4.50 mm

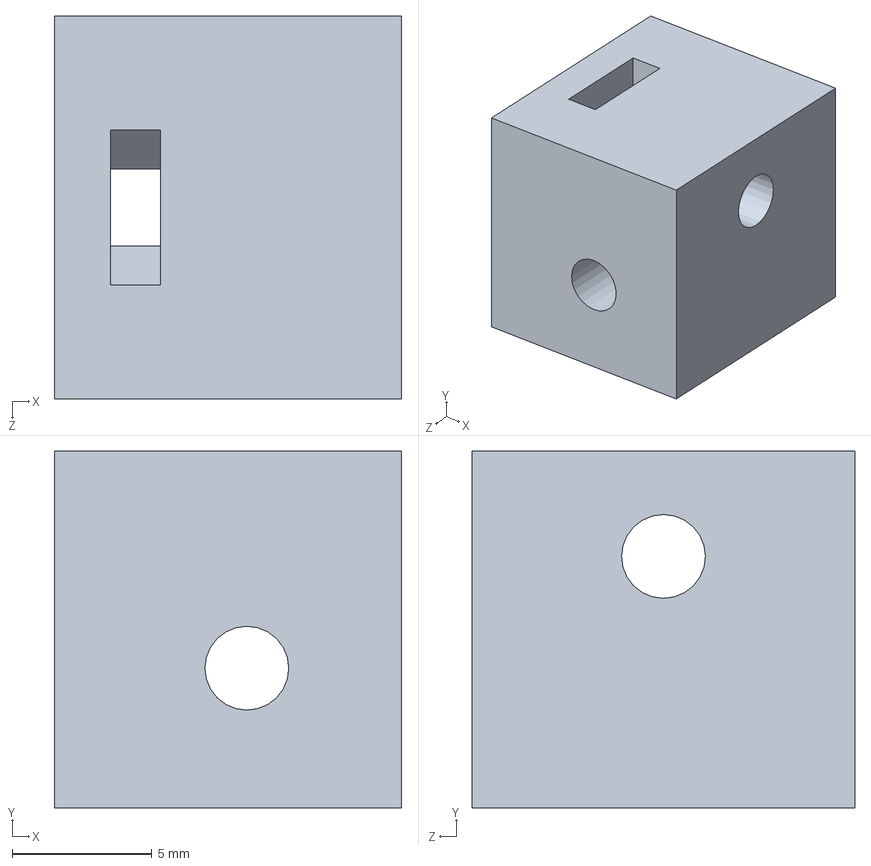
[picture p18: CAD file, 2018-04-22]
CAD/BlockBrackets/bracketBlockBottomEdge.SLDPRT
12.4 x 12.8 x 13.7 mm

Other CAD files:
CAD/FanMount-Wall.SLDPRT
CAD/Module Side Walls/OuterEdge-ModuleWall.SLDPRT
CAD/Motor Base and Covers/motorBase.SLDPRT
Laser Cut/InnerEdge-ModuleWall.DXF
CAD/Actuator Unit/leadscrew.SLDPRT
CAD/Actuator Unit/microMotor.SLDPRT
CAD/Actuator Unit/motorAttachment.SLDPRT
CAD/Actuator Unit/nut.SLDPRT
CAD/Actuator Unit/pin.SLDPRT
CAD/Actuator Unit/pinTop.SLDPRT
CAD/Actuator Unit/screwAndShaftAssembly.SLDASM
CAD/Base Components/BasePlate.SLDPRT
CAD/BlockBrackets/TopSupportBracket.SLDPRT
CAD/BlockBrackets/TopSupportSpacer.SLDPRT
CAD/BlockBrackets/bracketBlockBottomMiddle.SLDPRT
CAD/BlockBrackets/bracketBlockMiddle.SLDPRT
CAD/BlockBrackets/bracketBlockTop.SLDPRT
CAD/External Components/13135A590_BRACKET-PDB.SLDPRT
CAD/Module Side Walls/InnerEdge-ModuleWall.SLDPRT
CAD/Module Side Walls/InnerMiddle-ModuleWall.SLDPRT
CAD/Module Side Walls/OuterMiddle-ModuleWall.SLDPRT
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

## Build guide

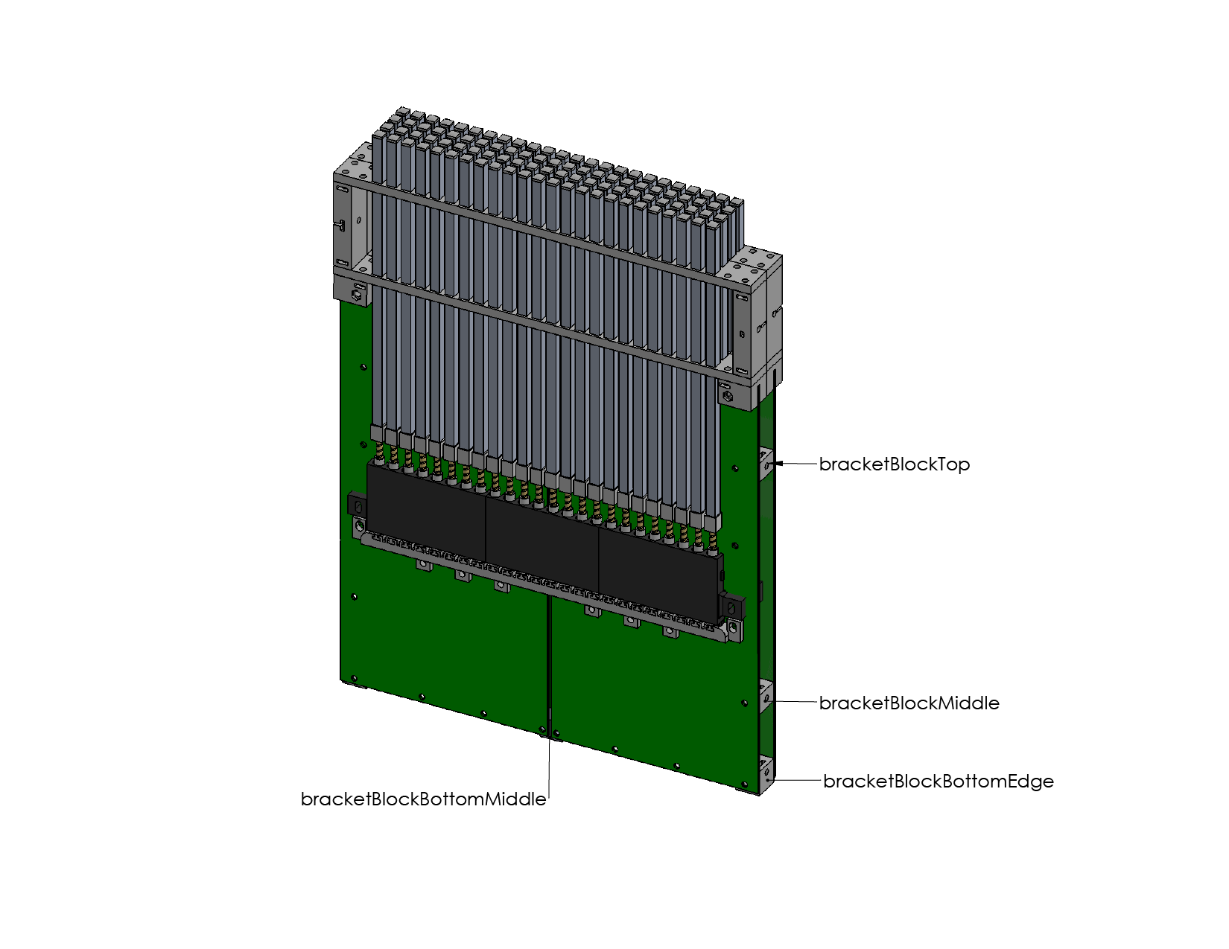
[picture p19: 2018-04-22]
Drawings/ModuleAssemblyDrawing-01.png

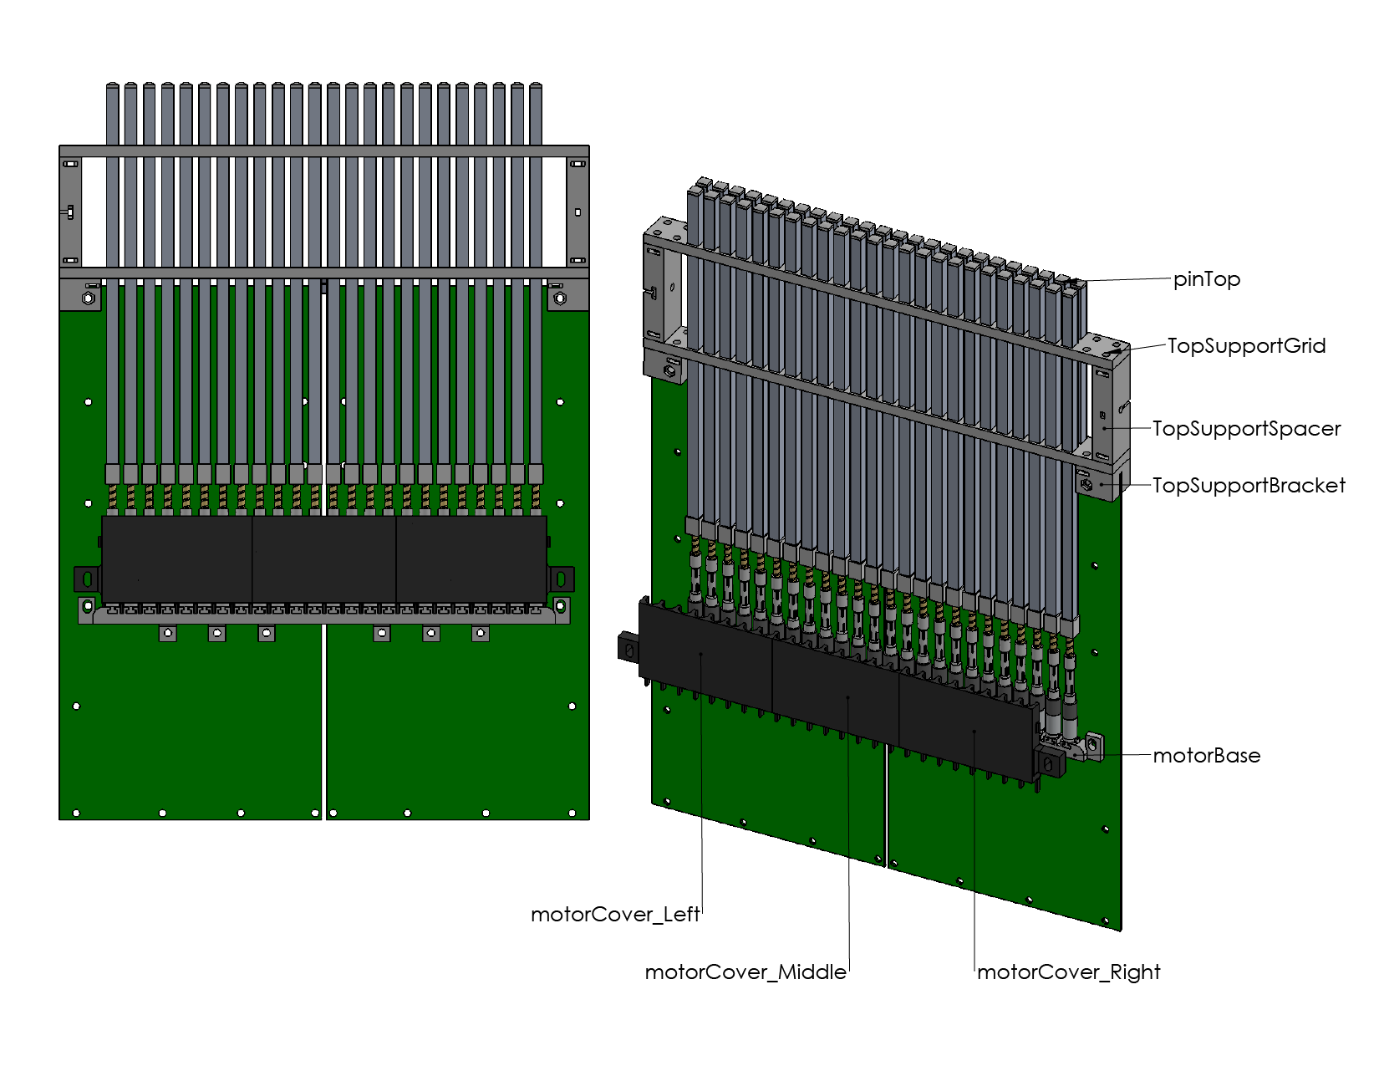
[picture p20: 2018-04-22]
Drawings/HalfModuleAssembly-01.png

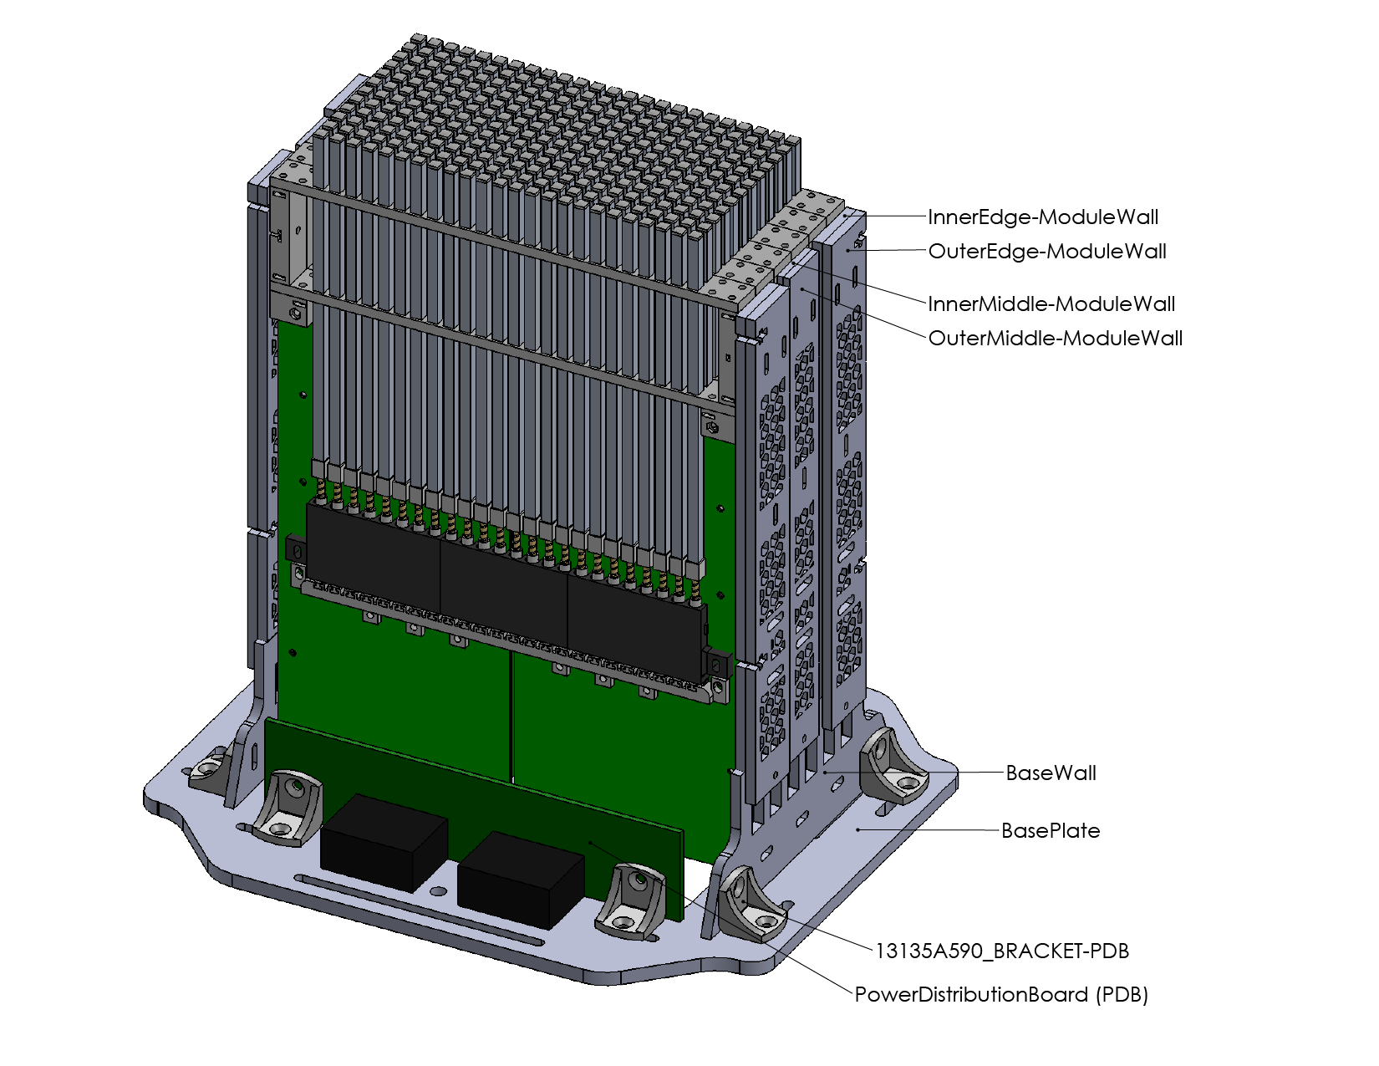
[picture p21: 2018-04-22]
Drawings/OverallAssemblyDrawing-01.png

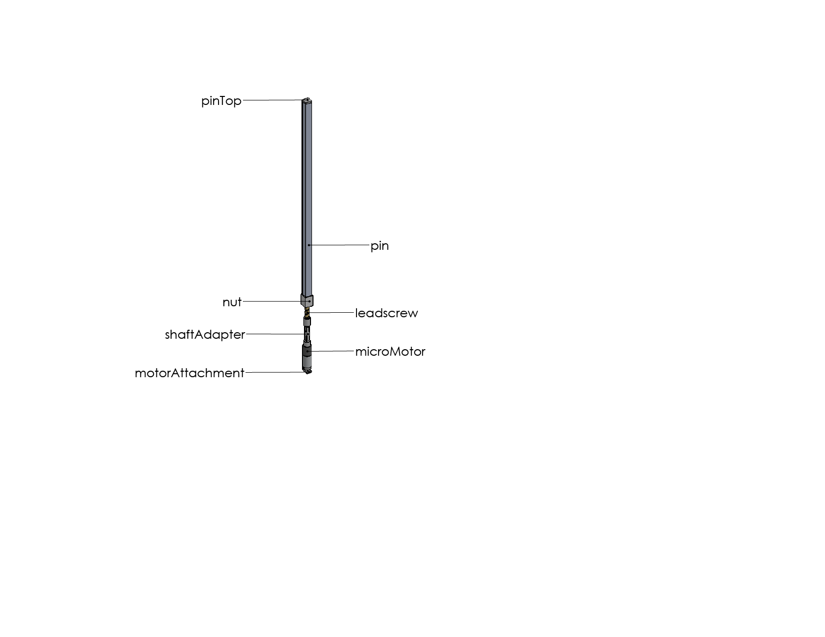
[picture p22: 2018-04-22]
Drawings/microMotorAssembly-01.png

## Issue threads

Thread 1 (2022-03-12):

Hard to find such small actuator

linchangyi1, 2022-03-12:
Hi! Thanks for your open source of shapeShift and I find the diameter of these actuators is only 6mm. However, it's hard for me to find such small actuators. Therefore, could you please tell me the website about the actuators you used in the project. Thank you very much for reading.

sfollmer, 2022-03-12:
https://www.robotshop.com/en/tiny-6mm-dc-coreless-motor-with-planetary-gearbox-3v-1200rpm.html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

On Sat, Mar 12, 2022 at 6:19 AM linchangyi1 ***@***.***>
wrote:

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
--
Sean Follmer, Ph.D. (he/him)
Assistant Professor
Mechanical Engineering: Design Group
Stanford University

***@***.***
shape.stanford.edu

linchangyi1, 2022-03-13:
Thank you very much for your reply.
Best wishes

linchangyi1, 2022-03-20:
Hi! I am sory to disturb you again. It seems that you control the motor with PID, but there is not encoder with the motor or in the CAD models. Could you please tell me how you get the feedback signal. Besides, are shaftAdapter, nut in the Actuator Unit directory made by 3D printer. And could you please the link to buy the leadscrew. Thank you for your time replying me.
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

alexasiu, 2022-03-23:
Hello, the shaftAdapter.SLDPRT has encoder marks which are used for determining position. This part couples the motor to the leadscrew and stands in front of two optical encoders to read position, the signal is what you would expect from a quadrature encoder. We can then count CW and CCW rotations and based on the lead screw pitch and diameter we can convert to linear position.

alexasiu, 2022-10-11:
Hello, the shaftAdapter.SLDPRT has encoder marks which are used for
determining position. This part couples the motor to the leadscrew and
stands in front of two optical encoders to read position, the signal is
what you would expect from a quadrature encoder. We can then count CW and
CCW rotations and based on the lead screw pitch and diameter we can convert
to linear position.

On Sun, Mar 20, 2022 at 5:25 AM linchangyi1 ***@***.***>
wrote:

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

Closed 2022-03-13.

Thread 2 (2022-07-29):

Cannot find a couple of CAD files

davisadrake, 2022-07-29:
Firstly, thank you for sharing this project! I was having some trouble opening the SolidWorks assemblies. Some of the files were saved in different folders than SolidWorks expected, but I was able to locate their new location. However, I was unable to find a couple of the files, resulting in errors. Here is the report SolidWorks gave me when opening the OverallAssembly:

_Instance of the following were suppressed or opened from new location when this file was opened

File	Reason
C:\Users\King of VR\Google Drive\Shape Lab\Projects\High Resolution Display\CAD-Files\prototype_v26.0\PCB_Export\PCB1.SLDASM	Unable to locate the file
D:\googleDrive\Shape Lab\Projects\High Resolution Display\CAD-Files\prototype_v27.0\bridgeSupport.SLDPRT	Unable to locate the file_

It seems that these prototype folders are missing from the github. Is it possible that the files "bridgeSupport" and "PCB_Export" are saved under different names?

Also, would you see any reason that the vertical travel range of the pins couldn't be increased to 150mm? Obviously this would require longer lead screws and extended pin supports.

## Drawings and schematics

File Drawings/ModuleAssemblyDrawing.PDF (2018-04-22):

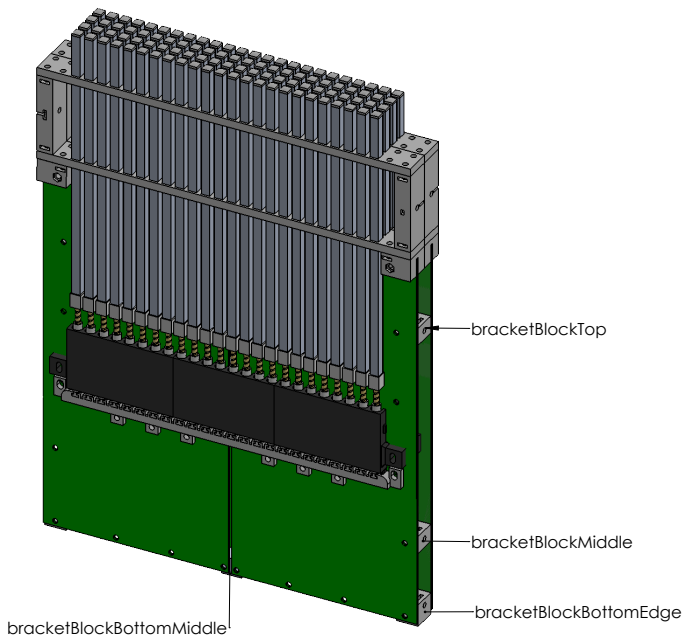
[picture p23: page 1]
bracketBlockBottomEdge bracketBlockBottomMiddle

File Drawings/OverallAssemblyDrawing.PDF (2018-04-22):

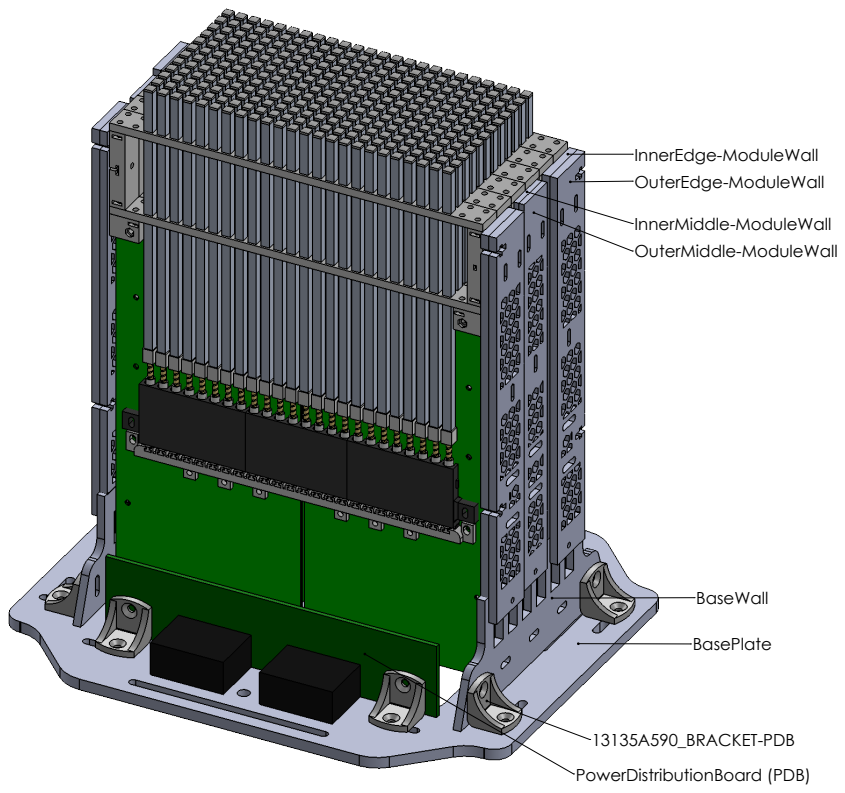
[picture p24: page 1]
PowerDistributionBoard (PDB)

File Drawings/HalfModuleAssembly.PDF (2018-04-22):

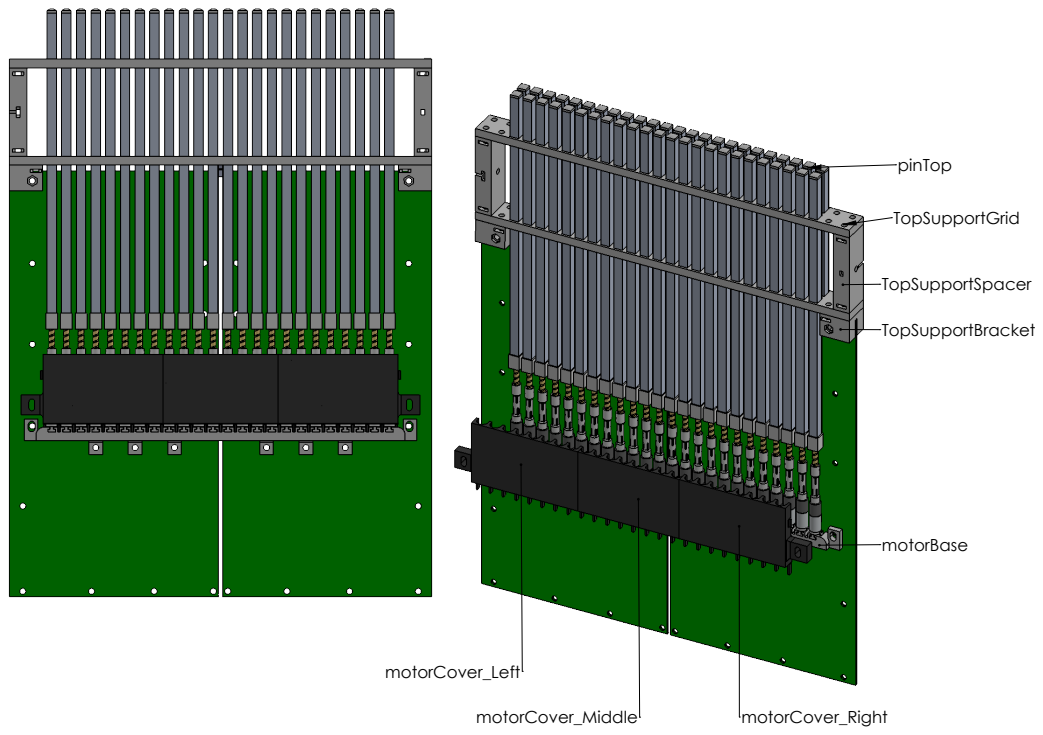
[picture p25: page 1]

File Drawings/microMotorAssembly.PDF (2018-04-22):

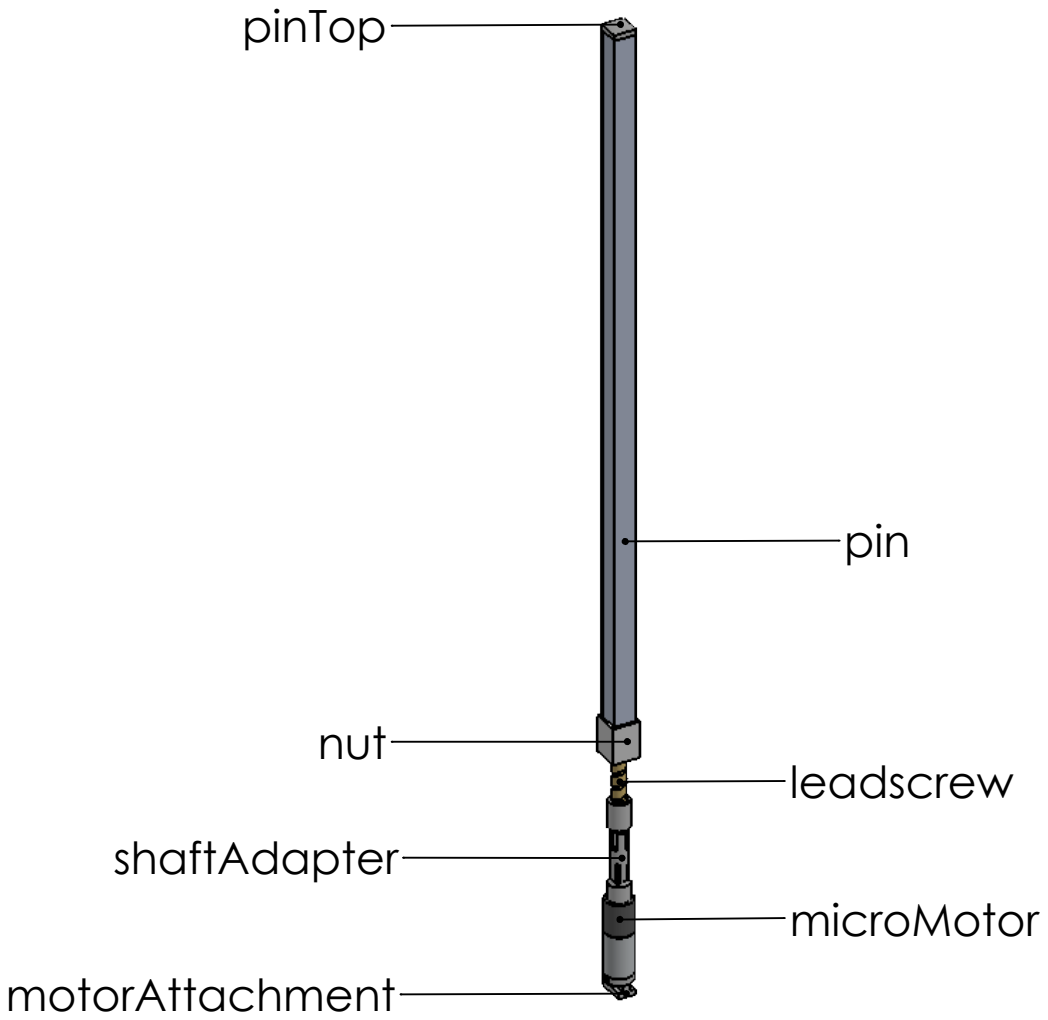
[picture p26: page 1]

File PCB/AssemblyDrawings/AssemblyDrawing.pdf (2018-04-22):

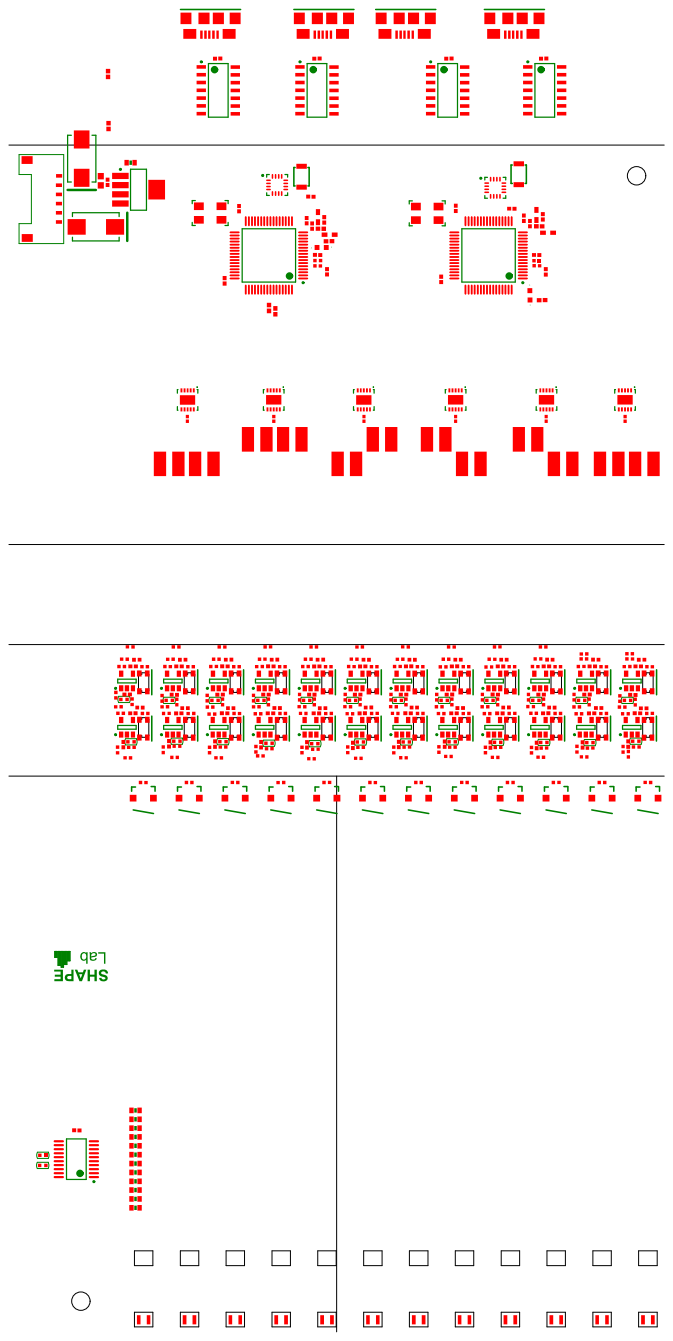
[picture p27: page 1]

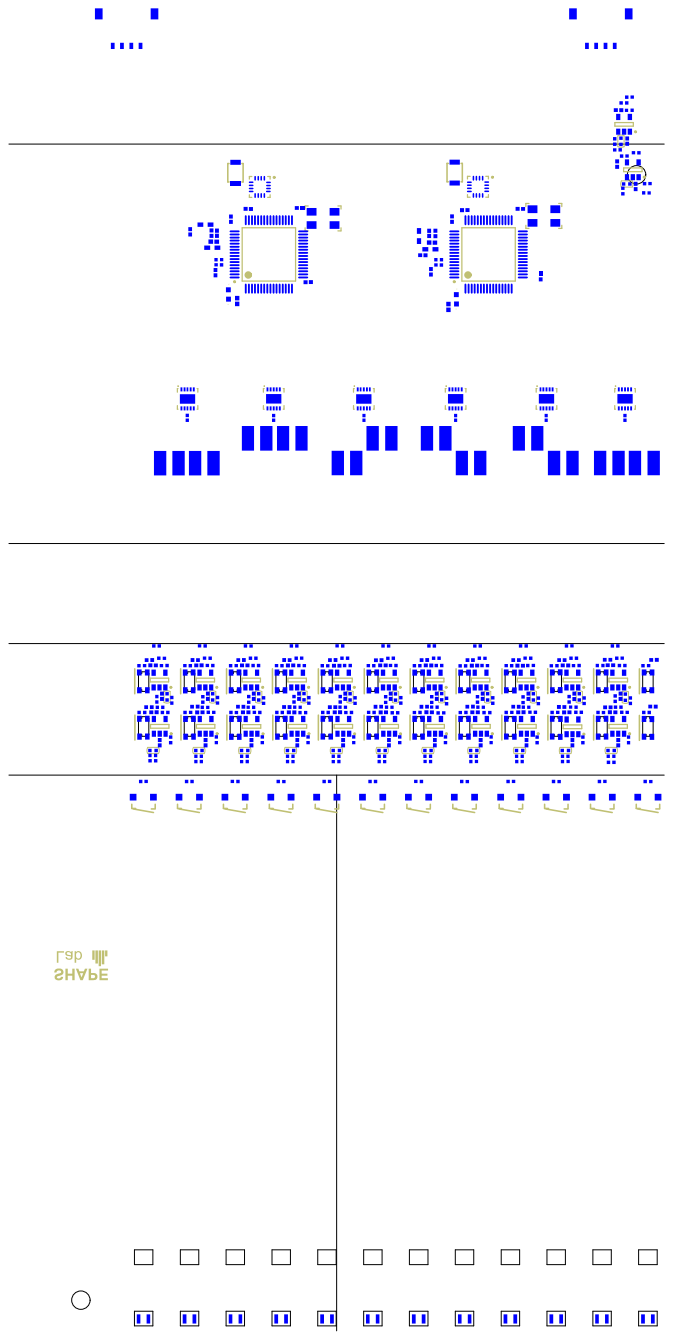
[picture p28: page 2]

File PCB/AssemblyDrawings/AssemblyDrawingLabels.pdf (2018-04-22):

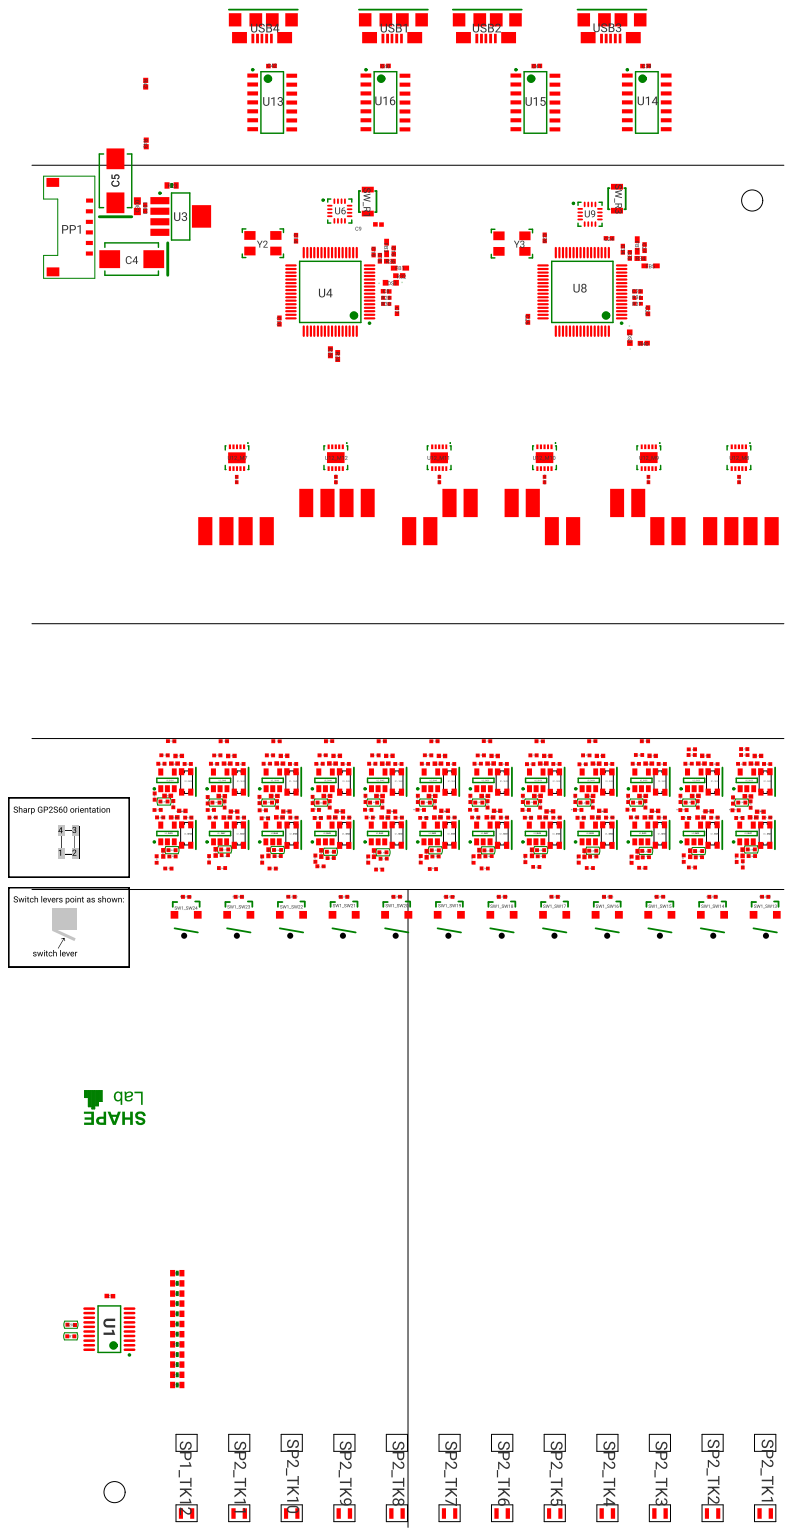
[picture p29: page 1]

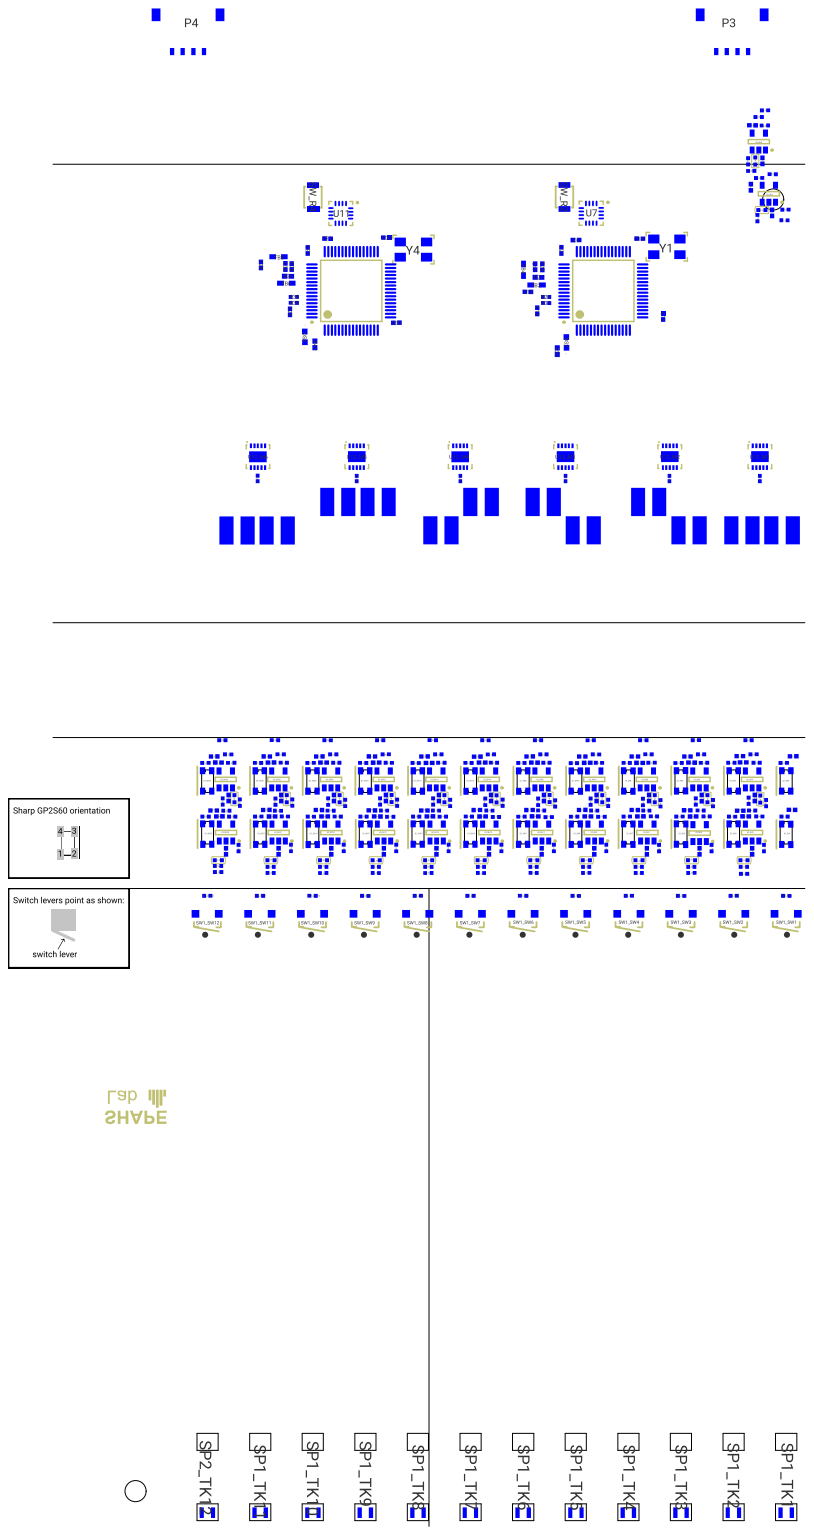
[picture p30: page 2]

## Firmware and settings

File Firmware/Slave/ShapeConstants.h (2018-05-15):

/****************************************************************************

  Header file for ShapeConstants.h
  Constants used by the shape display

 ****************************************************************************/
 
#ifndef _HIGH_RES_TEENSY_CONSTANTS_H
#define _HIGH_RES_TEENSY_CONSTANTS_H

// If using 3-tick encoder change PULSES_3 to 1
// Else set to 0
#define PULSES_3  0
#if PULSES_3
  #define PULSES_4  0
#else 
  #define PULSES_4  1
#endif

#define NUM_MOTORS      6

// optimmize encoder readings
#define ENCODER_USE_INTERRUPTS
#define ENCODER_OPTIMIZE_INTERRUPTS    

//------------RS485 Definitions & Variables-----------------
#define RS485Serial Serial1    // Using hardware serial for Teensy
#define SSerialRX        0     // Serial Receive pin
#define SSerialTX        1     // Serial Transmit pin
#define SSerialTxControl MK26  // RS485 Transmit control
// SSerialRxControl is tied to GND so device
// is always receiving
#define RS485Transmit    HIGH
#define RS485Receive     LOW
#define MAX_MSG_SIZE 8   // Max buffer size
#define MSG_LENGTH 8
#define MASTER_ID 65                  // Master Teensy ID
#define UNIVERSAL_SLAVE_ID 255        // Universal ID

// RS485 MSG IDs 
#define MSG_ADDR 0  // bit 0 is the slave ID
#define MSG_CMD  1  // bit 1 is the msg command/function
#define MSG_DATA 2  // bit 2 and higher is any data

// RS485 MSG ACTIONS
#define SET_POS         	254   // set pins position
#define SET_KP       		  253   // set Kp gain
#define ZERO_MOTORS     	252   // re-zero the motors
#define STOP_MOTORS     	251   // stop motors
#define SET_DEADZONE    	250   // set deadzone
#define SET_MAXSPEED    	249   // set max pin speed (0-255)
#define SET_MINSPEED      248   // set max pin speed (0-255)
#define SET_KI				    247	  // set Ki gain
#define SET_KD				    246   // set Kd gain
#define DISABLE_PIN       245   // disable pin
#define SET_MAX_TRAVEL    244   // disable pin

//----------Translation Definitions & Variables-----------
#define UP                 1
#define DOWN               -1
#define DEBOUNCE_DELAY     1
#define SWITCH_THRESH      700  // HIGH threshold for analog switches 
#define DEFAULT_SPEED      250
#define DEFAULT_MAX_TRAVEL 60

// Rotary to linear conversion variables
#if PULSES_3 // number of marks in the encoder
  #define PULSES_PER_REV  3.0f   
#elif PULSES_4
  #define PULSES_PER_REV  4.0f   
#endif
#define SCREW_PITCH     3.0f   // [mm/rev]
#define ZERO_OFFSET     -10  // switch position [mm]
#define ZERO_POS        0

// Stall-check variables
#define STALL_TIME      2000 // stall time threshold in ms
#define MAX_ZERO_TIME   6000 // max time for zeroing in ms   

// Conversion Factors - Multiply to convert e.g. 8 mm * MM_TO_PULSE = X pulses 
#define PULSE_TO_MM     ((1.0f/ ( PULSES_PER_REV / SCREW_PITCH )) * (1 / 4.0f)) // [mm/pulse]
#define MM_TO_PULSE     1/PULSE_TO_MM  //[pulse/mm]

// Threshold for special case switch connected to analog pin
#define ANALOG_SW_THRESH 950

#endif

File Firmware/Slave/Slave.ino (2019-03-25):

 /****************************************************************************
 Module
   Slave.ino

 Revision
   4.0.0

 Description  
    Script for slave microcontrollers in the shape display. 
    Handles 6 pins.

 Author
    Alexa Siu <afsiu@stanford.edu>
  
 History
 When             Who     What/Why
 --------------   ---     --------
****************************************************************************/

#include "ShapePin.h"
#include "ShapeConstants.h"
#include "Teensy-pin.h"      // Teensy pin definitions
#include "RS485_protocol.h"  // library with error-checking protocol
#include <EEPROM.h>

//-----------EEPROM Definitions & Variables-----------------//
int EEPROMAddress = 0;
byte myID = EEPROM.read(EEPROMAddress);       // Slave address
Mapping mapping(myID);                        // Map pins based on Slave ID

// Switch ISR
volatile bool switchStatus[6] = {false, false, false, false, false, false};
bool lastSwitchStatus[6] = {false, false, false, false, false, false};
typedef void (*GenericSwitchISR)(void);
GenericSwitchISR switchISR[6] = { &Switch0_ISR, &Switch1_ISR, &Switch2_ISR,
                                  &Switch3_ISR, &Switch4_ISR, &Switch5_ISR
                                };                          

//----------ShapePins -----------//
ShapePin pins[NUM_MOTORS] = {
  ShapePin ( 0, true, mapping.pin_motor[0], mapping.pin_motor[1],
  mapping.pin_encoder[0], mapping.pin_encoder[1] ),
  ShapePin ( 1, true, mapping.pin_motor[2], mapping.pin_motor[3],
  mapping.pin_encoder[2], mapping.pin_encoder[3] ),
  ShapePin ( 2, true, mapping.pin_motor[4], mapping.pin_motor[5],
  mapping.pin_encoder[4], mapping.pin_encoder[5] ),
  ShapePin ( 3, true, mapping.pin_motor[6], mapping.pin_motor[7],
  mapping.pin_encoder[6], mapping.pin_encoder[7] ),
  ShapePin ( 4, true, mapping.pin_motor[8], mapping.pin_motor[9],
  mapping.pin_encoder[8], mapping.pin_encoder[9] ),
  ShapePin ( 5, true, mapping.pin_motor[10], mapping.pin_motor[11],
  mapping.pin_encoder[10], mapping.pin_encoder[11] )
};

// Serial commands
const int bytes2Read = 5;
char inputArr[bytes2Read];  // store user input here     
int numRcvd;      
int cmd;
int pinNum;
int target;
const char delim[2] = "-";
const int singlePinSpeed = 255;
// commands for moving single pin
#define MOVE_PIN        1
#define STOP_PIN        2
#define ZERO_PIN        3
#define MOVE_ALL_PINS   4
#define STOP_ALL_PINS   5
#define ZERO_ALL_PINS   6

void setup() {
  Serial.begin(115200);  
  Serial.setTimeout(2);
  delay(1000);
  setupRS485();

  // setup switches and interrupt
  setupSwitches();

  Serial.println("Shape Display Firmware v04: Slave");
  Serial.printf( "Slave ID: %d\n", myID);
  #if PULSES_3
    Serial.println("Encoder: 3-ticks");
  #elif PULSES_4
    Serial.println("Encoder: 4-ticks | 03/14/2018");
  #else
    Serial.println("Encoder: error");
  #endif 
  Serial.println("-------------------------------------------\n");
}

void loop() {
  // read any messages from RS485
  readMSG();

  // analog switches need to be polled
  updateAnalogSwitches();

  // run the pins state machine
  RunPinsSM();

} //end loop

// read serial in case we don't want to use RS485 
// Command format: cmd-pinNum*-target*
//          *denotes optional parameters
// Serial commands:
//  - Move one pin: 1-pinNum-(1,2,or 3) 
//    1 will move the pin to 20 mm 
//    2 will move the pin to 35 mm
//    3 will move the pin to 50 mm
//  - Stop one pin: 2-pinNum
//  - Zero one pin: 3-pinNum
//  - Move all pins: 4
//  - Stop all pins: 5
//  - Zero all pins: 6
void readSerial() {
  
    // read user input
    numRcvd = Serial.readBytes( inputArr, bytes2Read );
    // cmd-pinNum-target*

    char *token;
    // check if we received the correct data
    if ( numRcvd > 0 ) {
      
      Serial.print("received cmd: ");
      Serial.println(inputArr);
    
      // first get the cmd byte
      token = strtok(inputArr, delim);
      cmd = atoi(token);

      int targetPos = 0;
      
      // cmd is target position
      switch ( cmd ) {
        case MOVE_PIN:
          token = strtok(NULL, delim);
          pinNum = atoi( token );
          token = strtok(NULL, delim);
          target = atoi( token );
          if ( pinNum >= 0 && pinNum < NUM_MOTORS ) {
            if (target == 1) {
              targetPos = 20;
              pins[pinNum].CommandTargetPos(targetPos);
            } else if (target == 2) {
              targetPos = 35;
              pins[pinNum].CommandTargetPos(targetPos);
            } else if (target == 3) {
              targetPos = 50;
              pins[pinNum].CommandTargetPos(targetPos);
            } 
            Serial.printf("pin %d, target %d\n", pinNum, targetPos);
          } else {
            Serial.printf("cmd for invalid pin num %d. Pin num should be between 0-5\n", pinNum);
          }
          
        break;
        case STOP_PIN:          
          token = strtok(NULL, delim);
          pinNum = atoi( token );
          if ( pinNum >= 0 && pinNum < NUM_MOTORS ) {
            pins[pinNum].Idle();
            Serial.printf("stop pin %d\n", pinNum);
          } else {
            Serial.printf("stop cmd for invalid pin num %d. Pin num should be between 0-5\n", pinNum);
          }
        break;
        case ZERO_PIN:
          token = strtok(NULL, delim);
          pinNum = atoi( token );
          if ( pinNum >= 0 && pinNum < NUM_MOTORS ) {
            pins[pinNum].Zero();
            Serial.printf("zero pin %d\n", pinNum);
          } else {
            Serial.printf("zero cmd for invalid pin num %d. Pin num should be between 0-5\n", pinNum);
          }
        break;
        case MOVE_ALL_PINS:
          token = strtok(NULL, delim);
          target = atoi( token );
          if (target == 1) {
            targetPos = 20;
            CommandPins(targetPos);
          } else if (target == 2) {
            targetPos = 35;
            CommandPins(targetPos);
          } else if (target == 3) {
            targetPos = 50;
            CommandPins(targetPos);
          } 
          Serial.printf("moving all pins to %d\n", targetPos);
        break;
        case STOP_ALL_PINS:
          StopPins();
          Serial.printf("stopping all pins\n");
        break;
        case ZERO_ALL_PINS:
          ZeroPins();
          Serial.printf("zeroing all pins\n");
        break;
      }
      Serial.println("");
      Serial.flush();
    }
  
}

// Command all pins
void CommandPins ( int newPos ) {
  for (int i = 0; i < NUM_MOTORS; i++) {
    pins[i].CommandTargetPos( newPos );
  }
}

// Zero all pins
void ZeroPins ( void ) {
  for (int i = 0; i < NUM_MOTORS; i++) {
    pins[i].Zero();
  }
}

// Stop all pins
void StopPins ( void ) {
  for (int i = 0; i < NUM_MOTORS; i++) {
    pins[i].Idle();
  }
}

// Run state machine for all pins
void RunPinsSM ( void ) {
  // run each pin's state machine
  for (int i = 0; i < NUM_MOTORS; i++) {
    pins[i].RunSM();
  }
}

//----------------------Switch Functions-----------------------
void setupSwitches () {
  for (int i = 0; i < NUM_MOTORS; i++) {
    
    pinMode( mapping.pin_switch[i], INPUT ); 
    
    // If we're using an MCU with analog switches (MCU_ID is 0)
    if ((myID % 4 == 3) && ( (i == 0) || ((i == 4) || (i == 5)))) {
      // Set analog switch status to true if above threshold
      pins[i].SwitchISR( analogRead(mapping.pin_switch[i]) > ANALOG_SW_THRESH );
    }
    // Otherwise read digitally
    else {
      if ( digitalRead(mapping.pin_switch[i]) == HIGH ) {
        pins[i].SwitchISR(true);
      } else {
        pins[i].SwitchISR(false);
      }
      // Attach interrupts to digital switches
      attachInterrupt ( digitalPinToInterrupt(mapping.pin_switch[i]), switchISR[i], CHANGE);
    }
  } //endfor
  
}

// For analog switches, need to manually call 'ISR function'
void updateAnalogSwitches() {
  for (int i = 0; i < NUM_MOTORS; i++) {
    // If we're using an MCU with analog switches (MCU_ID is 0)
    if ((myID % 4 == 3) && ( (i == 0) || ((i == 4) || (i == 5)) ) ) {
      // Read analog switch status
      pins[i].SwitchISR( analogRead(mapping.pin_switch[i]) > ANALOG_SW_THRESH );
    }
  }
}

//---------------------RS485 Functions-----------------//
void setupRS485( void ) {
  pinMode(SSerialTxControl, OUTPUT);
  digitalWrite(SSerialTxControl, RS485Receive);  // Init Transceiver
  RS485Serial.begin(1000000);
}

// read messages sent through RS485
void readMSG() {
  byte msgReceived[MAX_MSG_SIZE]; // Create a buffer
  byte receivedMsgLen = receiveMsg(msgReceived);

  // declare variabless outside switch so compiler is happy
  int pinNum, newKp, newKi, newKd, newSpeed; 
  
  // Length of msg (length > 0 for real msg)
  if ( receivedMsgLen ) {
    // Then parse the msg
    // First check if it's a msg for this device
    if ( (msgReceived[MSG_ADDR] != myID) && (msgReceived[MSG_ADDR] != UNIVERSAL_SLAVE_ID) ) {
      //Serial.println("Message is not for me.");
      return; //return

      // Check it's a valid command
    } else if ( msgReceived[MSG_CMD] < 245 ) {
      //Serial.println("Not a valid command.");
      return;

      // Else it is for us and it is a valid command
    } else {
      // Get the command type
      byte msgCmd = msgReceived[MSG_CMD];
      // Based on the cmd type choose on of the cases:
      switch ( msgCmd ) {

        case SET_POS:   // Set new setpoints
          //Serial.println("Set positions.");
          for (int i = 0; i < NUM_MOTORS; i++) {
            pins[i].CommandTargetPos( int( msgReceived[MSG_DATA + i] ) );
            if ( i == 5 && myID%8 == 3 && msgReceived[MSG_DATA + i] > 30 ) {
              pins[i].CommandTargetPos( 25 );
            }
          }
          break;

        case SET_KP:  // Set PID gains
          //Serial.println("Set gains.");
          // PID PACKET STRUCTURE
          // [ID]  [CMD]  [PIN#]  [KP]

          pinNum = int(msgReceived[MSG_DATA]);
          newKp = int(msgReceived[MSG_DATA + 1]);		
          pins[pinNum].SetKp(newKp); 
          break;

        case SET_KI:  // Set PID gains
          // PACKET STRUCTURE
          // [ID]  [CMD]  [PIN#]  [KI]

          pinNum = int(msgReceived[MSG_DATA]);
          newKi = int(msgReceived[MSG_DATA + 1]);
          pins[pinNum].SetKi(newKi); 
          break;

        case SET_KD:  // Set PID gains
          // PACKET STRUCTURE
          // [ID]  [CMD]  [PIN#]  [KD]

          pinNum = int(msgReceived[MSG_DATA]);
          newKd = int(msgReceived[MSG_DATA + 1]);
          pins[pinNum].SetKd(newKd); 
          break;

        case SET_MAXSPEED:
          //  PACKET STRUCTURE
          // [ID]  [CMD]  [PIN#]  [SPEED]
          pinNum = int(msgReceived[MSG_DATA]);
          newSpeed = int(msgReceived[MSG_DATA + 1]);
          pins[pinNum].SetMaxSpeed(newSpeed); 
          break;

        case SET_MINSPEED:
          //  PACKET STRUCTURE
          // [ID]  [CMD]  [PIN#]  [SPEED]
          pinNum = int(msgReceived[MSG_DATA]);
          newSpeed = int(msgReceived[MSG_DATA + 1]);
          pins[pinNum].SetMinSpeed(newSpeed); 
          break;

        case DISABLE_PIN: 
          //  PACKET STRUCTURE
          // [ID]  [CMD]  [PIN#]  [GARBAGE]

          pinNum = int(msgReceived[MSG_DATA]);
          pins[pinNum].DisableShapePin(); 
          break;

        case ZERO_MOTORS:   // Re-zero motors
//          Serial.println("Zeroing motors.");
          ZeroPins();
          break;

        case STOP_MOTORS:   // Stop all motors
          //Serial.println("Stopping motors.");
          StopPins();
          break;

        case SET_DEADZONE:
          for (int i = 0; i < NUM_MOTORS; i++) {
            pins[i].SetDeadzone( int(msgReceived[MSG_DATA]) );
          }
          break;

        case SET_MAX_TRAVEL:
          for (int i = 0; i < NUM_MOTORS; i++) {
            pins[i].SetMaxTravel( int(msgReceived[MSG_DATA]) );
          }
        break;

      } //end switch
    } //endif valid cmd
  } //endif msg received
}

/*
    receiveMsg

    Description
      Receives RS485 message and saves it to
      the passed in byte array buffer

    Parameters
      Byte array where the received msg will
      be stored

    Returns
      0 if it was nothing, otherwise returns
      length of msg received

*/
byte receiveMsg(byte *msgBuffer) {
  //  return recvMsg (fAvailable, fRead, msgBuffer, sizeof msgBuffer);
  return recvMsg (fAvailable, fRead, msgBuffer, MSG_LENGTH, 8);
}

/*
    sendMsg

    Description
      Sends RS485 message from Master

    Parameters
      Message to send as a byte array

    Returns
      None

*/
void sendMsg( byte* msg ) {
  // Enable the transmit pin
  RS485Serial.transmitterEnable(SSerialTxControl);
  // Send the message
  sendMsg (fWrite, msg, sizeof msg);
}

/*
    printByteArray

    Description
      Print a byte array msg to the serial monitor

    Parameters
      Takes a byte array with the message to
      print

    Returns
      None
*/
void printByteArray(byte arr[], int len) {
  Serial.print( "msg: " );
  for ( int i = 0; i < len; i++ ) {
    Serial.print( arr[i] );
    Serial.print(" " );
  }
  Serial.println(".");
} // end printByteArray

/*
    fWrite

   Callback functions used by RS495_protocol
   to write to RS485 hardware serial

*/
void fWrite (const byte msg) {
  RS485Serial.write (msg);
}

/*
   fAvailable

   Callback functions used by RS495_protocol
   to check if there's any bytes being transmitted

*/
int fAvailable () {
  return RS485Serial.available();
}

/*
   fRead

   Callback functions used by RS495_protocol
   to read from RS485 hardware serial

*/
int fRead () {
  return RS485Serial.read();
}

//--------------------- Switch ISR -----------------//
void Switch0_ISR ( void ) {
  if ( digitalRead(mapping.pin_switch[0]) == LOW ) {
    pins[0].SwitchISR(false);
  } else {
    pins[0].SwitchISR(true);
  }
}


void Switch1_ISR ( void ) {
  if ( digitalRead(mapping.pin_switch[1]) == LOW ) {
    pins[1].SwitchISR(false);
  } else {
    pins[1].SwitchISR(true);
  }
}

void Switch2_ISR ( void ) {
  if ( digitalRead(mapping.pin_switch[2]) == LOW ) {
    pins[2].SwitchISR(false);
  } else {
    pins[2].SwitchISR(true);
  }
}

void Switch3_ISR ( void ) {
  if ( digitalRead(mapping.pin_switch[3]) == LOW ) {
    pins[3].SwitchISR(false);
  } else {
    pins[3].SwitchISR(true);
  }
}

void Switch4_ISR ( void ) {
  if ( digitalRead(mapping.pin_switch[4]) == LOW ) {
    pins[4].SwitchISR(false);
  } else {
    pins[4].SwitchISR(true);
  }
}

void Switch5_ISR ( void ) {
  if ( digitalRead(mapping.pin_switch[5]) == LOW ) {
    pins[5].SwitchISR(false);
  } else {
    pins[5].SwitchISR(true);
  }
}

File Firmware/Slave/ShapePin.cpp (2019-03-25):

/****************************************************************************
 Module
   ShapePin.cpp

 Revision
   2.0.0

 Description
   Library for a shape display pin

 Notes
 
 Author
    A. Siu <afsiu@stanford.edu>
   
 History
 When           Who     What/Why
 -------------- ---     --------
 05/18/17 10:30 afs     first pass
 05/19/17 15:04 afs     most functions but interrupts for switch
 05/22/17 21:44 afs     integrated with main function + interrupts
 05/24/17 04:50 afs     wrote our own PID library
 05/25/17 19:40 afs     tested with high gear and low gear ratio motors
 05/31/17 14:11 afs     pins initial state is now idle
 06/29/17 16:28 afs     zeroing now uses pid loop
****************************************************************************/

/*----------------------------- Include Files -----------------------------*/
#include "ShapePin.h"

/*----------------------------- Module Defines ----------------------------*/
#define ENCODER_OPTIMIZE_INTERRUPTS
#define ENCODER_USE_INTERRUPTS

/****************************************************************************

  Public Functions

****************************************************************************/

/****************************************************************************
 Function
    ShapePin

 Parameters
  motorApin: pin for motor lead A
  motorBpin: pin for motor lead B 
  encoderApin: pin for TOP encoder **direction!! otherwise encoder readings will be off
  encoderBpin: pin for BOTTOM encoder
  switchPin: pin for the limit switch
  analog: true if this pin has switch on an analog pin 

 Returns
    None

 Description
    Constructor. Sets the motor, encoder, and switch pins.

 Author
     A. Siu, 05/18/17, 5:00
****************************************************************************/
ShapePin::ShapePin ( int id, bool enabled, int motorA, int motorB, 
                     int encoderA, int encoderB ) 
{
  // initialize variables
  pinID = id;
  pinEnabled = enabled;
  motorApin = motorA;
  motorBpin = motorB;
  encoderApin = encoderA;
  encoderBpin = encoderB;

  /* Control variables */
  targetPos = 0;
  pid_output = 0;
  // Values that work 
  Kp = 1500; //60;  //60 //60;
  Kd = 200;  //40;  //30 //35;
  Ki = 5;    //2;   //3 //25;
  SetDeadzone( 1 ); //[mm]
  SetMaxTravel( DEFAULT_MAX_TRAVEL ); 
  
  // set pins as output/input
  pinMode( motorApin, OUTPUT );
  pinMode( motorBpin, OUTPUT );

  // start with motors off
  Stop();

  // initialize encoder object
  encoder = new Encoder(encoderApin, encoderBpin);

  // set PID mode and limits
  motorPID = new PID( Kp, Ki, Kd );
  motorPID->SetOutputLimits(-DEFAULT_SPEED, DEFAULT_SPEED);
  // sampleTime = speed * res = 75mm/s * 1/0.25mm = 60Hz --> 1/60=0.0167 --> 3.3 ms
  motorPID->SetSampleTime(2);

  // start initially IDLE
  currentPinState = IDLE;

  /* Stall check variables */
  isTraveling = true;
  travelStartTime = millis(); // [ms]
  lastTargetPos = 0.0;        // [pulses]
  travelStartPosition = 0.0;  // [pulses]
}

/****************************************************************************
 Function
    RunSM

 Parameters
    None

 Returns
    None

 Description
    Act according to pin's current state.

 Author
     A. Siu, 05/18/17, 5:00
****************************************************************************/
void ShapePin::RunSM( void ) {
 
  switch (currentPinState) {
    case IDLE:
      Stop();
    break;

    case WAITING4SWITCH:
      CheckSwitch();
      // check if pin is jammed
      CheckIfStalledZeroing();
    break;

    case MOVING2TARGET:
      // Check switch
      CheckSwitch();
      // run PID to move pin
      RunControlLoop();
      // Check if the pin has been stalled
      CheckIfStalled();
    break;

    /// The states below are mostly for debugging ///
    case UP_STATE:
      Move( UP, 150 );
      //RunControlLoopWithoutMoving();
    break;
    
    case DOWN_STATE:
      Move( DOWN, 150 );
      //RunControlLoopWithoutMoving();
    break;

    case DEBUG:
      debug();
    break;
    /// end debug states
    
    default:
    break;
  } //end switch

  //debug();
  
}

void ShapePin::SetState( PinState_t newState ) {
  currentPinState = newState;
}

/****************************************************************************
 Function
  Zero

 Parameters
  None

 Returns
    None

 Description
  Re-zeros pin based on switch.

 Author
     A. Siu, 05/18/17, 5:00
****************************************************************************/
void ShapePin::Zero( void ) {
  currentPinState = WAITING4SWITCH;
  SetMaxSpeed(loweringSpeed);
  SetMinSpeed(loweringSpeed);
  // command pin to keep moving down
  CommandTargetPos ( GetPosMM() - 10000 );
  // keep track of time to check if stalled
  isTraveling = true;
  travelStartTime = millis();
}
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

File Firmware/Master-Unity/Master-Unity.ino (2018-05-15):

 /****************************************************************************
 Module
   Master-Unity.ino

 Revision
   4.0.0

 Description
    Script that talks through Serial to Unity program. 
    Based on Unity commands, it sends information to 
    the shape display hardware through RS485.

    Msg format from Unity: 
      Byte  0 : command byte (data, zero, stop, etc...)
      Byte 1-n: any data bytes

 Author
    Alexa Siu <afsiu@stanford.edu>
  
 History
 When             Who     What/Why
 --------------   ---     --------
****************************************************************************/
// Debug booleans | If true, system will have some significant delays
bool debug = false;         // true if want minimal print statements
bool debugData = false;     // true if want to print the data Teensy receives from unity
bool sendRS485msg = true;   // true if connected to RS485
bool ledOnSerialReceive = true;
bool ledOnRS485send = !ledOnSerialReceive;
unsigned long receivedMsgStartTime;

/// IMPORTANT to update these otherwise arrays will
//            random register values
// Set the physical display parameters
const int displaySizeX = 12;                        // number of rows
const int displaySizeZ = 24;                        // pins per row
const int displaySize = displaySizeX*displaySizeZ;  // display size
char zMap[displaySize];         // buffer to store data sent from Unity
int numRcvd;                    // keep count of how many bytes are received
const int setupSize = 4;              // size of setup command sent from Unity
char setupData[setupSize];      // buffer for storing setup command from Unity
#define PINS_PER_MCU 6

#include "RS485_protocol.h"  // library with error-checking protocol
#include <EEPROM.h>

// This board's address
int EEPROMAddress = 0;
byte myID = 0;

// SM states
typedef enum { SENDING, FORWARDING_SETUP, WAITING_2_RECEIVE, WAITING_4_CMD } MasterState_t;
MasterState_t currentState = WAITING_4_CMD;

// RS485 variables
#define RS485Serial Serial1 
#define SSerialRX        0     // Serial Receive pin
#define SSerialTX        1     // Serial Transmit pin
#define SSerialTxControl 2     // RS485 Transmit control
#define RS485Transmit    HIGH
#define RS485Receive     LOW

// Msg definitions
#define MAX_MSG_SIZE 63
#define MSG_LENGTH 8
#define SLAVE_ID 1
#define UNIVERSAL_SLAVE_ID 255

// Msg types from unity
#define DataCMD   127
#define ZeroCMD   126
#define StopCMD   125
#define SetupCMD  124

// Msg types for hardware slave
#define MSG_ADDR 0  // bit 0 is the slave ID
#define MSG_CMD  1  // bit 1 is the msg command/function
#define MSG_DATA 2  // bit 2 and higher is any data

// Msg commands for hardware slave
#define SET_POS           254   // set pins position
#define SET_KP            253   // set Kp gain
#define ZERO_MOTORS       252   // re-zero the motors
#define STOP_MOTORS       251   // stop motors
#define SET_DEADZONE      250   // set deadzone
#define SET_MAXSPEED      249   // set max pin speed (0-255)
#define SET_MINSPEED      248   // set max pin speed (0-255)
#define SET_KI            247   // set Ki gain
#define SET_KD            246   // set Kd gain
#define DISABLE_PIN       245   // disable pin

// LED for debugging
#define ledPin 13
bool ledOn = false;

void setup() {

  // Assign ID
  myID = EEPROM.read(EEPROMAddress);
  
  // Start the built-in serial port, probably to Serial Monitor
  Serial.begin(115200);
  
  // LED setup
  pinMode(ledPin, OUTPUT);  
  digitalWrite(  ledPin, HIGH );

  // RS485 setup
  pinMode(SSerialTxControl, OUTPUT);
  digitalWrite(SSerialTxControl, RS485Receive);  // Init Transceiver
  // Start the software serial port, to another device
  RS485Serial.begin(1000000); // set the data rate 
  delay(1000);
  
  // Unity setup
  // Initialize the buffer with 0s
  for ( int  i = 0; i < displaySize; i++ ) {
    zMap[i] = 0;
  }

  Serial.println(F("Teensy: Initialized shape display Master - v04"));

}

void loop() {
// Latency measurement
//  unsigned long lastTime = micros();
//  SendNewPositions();
//  Serial.printf("Time to send all pin position: %i micros \n", (micros() - lastTime));
//  Serial.println();

  
  switch ( currentState ) {

//    // Master will request the display size and won't do anything
//    // until this is received
//    case INIT:
//    break;

    // in this state the master will wait for a cmd from Unity
    // Current commands include:
    //  - DataCMD to update the pin positions
    //  - SetupCMD to forward setup parameters
    //  - ZeroCMD to reset the display back to all zeros
    //  - StopCMD to stop and reset the display 
    case WAITING_4_CMD:
      numRcvd = 0;
      char cmd[1];
      // Read the bytes from serial
      // Expecting bytes to be equal to one cmd byte
      
      numRcvd = Serial.readBytes( cmd, 1 );
      if ( numRcvd > 0 ) {
        if ( ledOnSerialReceive ) {
          digitalWrite( ledPin, HIGH ); 
        }
        if (  ( (int)cmd[0] )  == DataCMD ) {
          if (debug) {
            receivedMsgStartTime = micros();
            Serial.println( F("Teensy: Received a data cmd.") );
          }
          currentState = WAITING_2_RECEIVE;
          break;
        } else if (  ( (int)cmd[0] ) == SetupCMD ) {
          if ( debug ) {
            Serial.println( F("Teensy:  Received a setup cmd.") );
          }
          currentState = FORWARDING_SETUP;
        } else if (  ( (int)cmd[0] ) == ZeroCMD ) {
          if ( debug ) {
            Serial.println( F("Teensy:  Received a zeroing cmd.") );
          }
          ZeroDisplay();
        } else if (  ( (int)cmd[0] )  == StopCMD ) {
          if ( debug ) {
            Serial.println( F("Teensy: Received a stop cmd.") );
          }
          StopDisplay();
        } 
      } //endif
      //Serial.flush();  // clear the buffer
      if ( ledOnSerialReceive ) {
        digitalWrite( ledPin, LOW );
      }
    break;

    // wait for setup commmand from unity, forward the message when received
    case FORWARDING_SETUP:
    
      numRcvd = 0;
      // Read the bytes from serial into setup data buffer
      // Expecting bytes to be equal to setupSize 
       numRcvd = Serial.readBytes( setupData, setupSize );
      // Check-sum to ensure correct amount of data was received
      if ( numRcvd == setupSize ) {
        if ( debug ) {
          Serial.printf( F("Teensy: received %i setup bytes for Slave %i.\n"), numRcvd, (int)setupData[0] );
          Serial.printf( F("Teensy: Sending setup msg: %i %i %i %i.\n"), (int)setupData[0], (int)setupData[1], (int)setupData[2], (int)setupData[3]);
        }
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

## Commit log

2018-04-22 first pass pcb + cad files
    [13135A590_BRACKET-PDB.SLDPRT, 80mm PC fan.SLDASM, BOM_PartType-ShapeDisplay-V6.xls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]
2019-01-22 included dxf files for laser cutting
    [BasePlate.DXF, BaseWall.DXF, FanMount-Wall.DXF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]
2019-03-25 new laser cut files and improved firmware
